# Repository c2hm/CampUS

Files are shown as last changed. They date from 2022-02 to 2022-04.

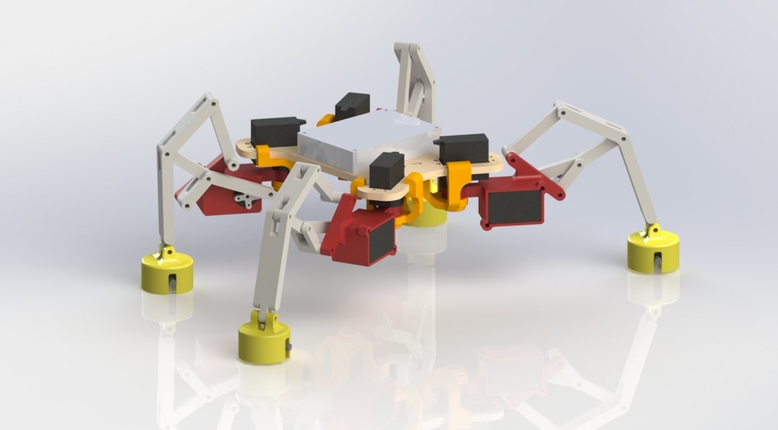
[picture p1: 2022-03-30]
Conception/Prototype #2/vue isometrique (2).JPG

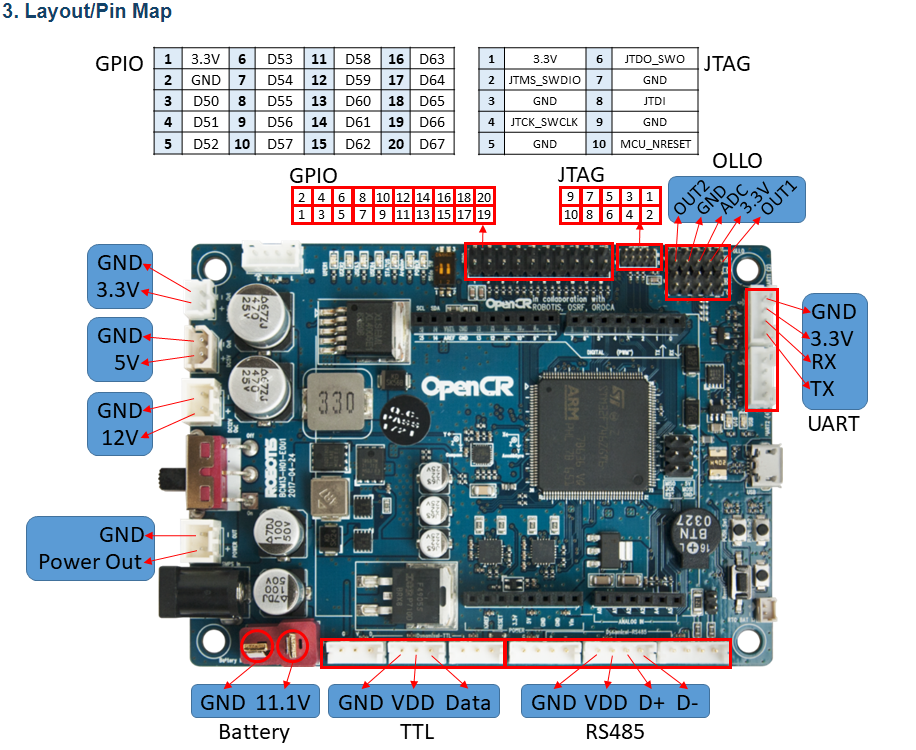
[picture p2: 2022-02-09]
Electricity/pins OpenCR.png

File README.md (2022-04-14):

# CampUS
University of Sherbrooke robotics project
  
  Isometric view
  
The CampUS robot is a quadriped articulated robot. Each leg is independent and contains two degrees of freedom, but all of these allow the robot to move from all sides.   An electromagnet is attached to each leg to allow the robot to move on metal surfaces. All components are controlled by an OpenCR card programmed in C++. This program handles the low-level commands needed for the move. A user interface is used to communicate to the robot the sequences of high-level movements to be executed according to the user's intention. A Bluetooth module makes it possible to make the wireless link between the two programs. 

The diagram below summarizes the general architecture explained above:

 

Here is a demonstration of the robot : 40 cm at 0°, 20 cm at 10° and 20 cm at -10°  

https://user-images.githubusercontent.com/61423054/163423675-e28aa425-6067-4ee7-8b0e-fbca73a94658.mp4

# Code

  This folder contains all the code for Python interface and the C++ Arduino controller code
  
# Conception 

  This folder contains all the prototypes created on SolidWorks and the complete assembly manual of the mechanical and electrical parts

# Demo 

  This folder contains all the videos of movement to see the motion in detail
  
# Electricity

  This folder contains the information about the OpenCR board, the protoboard and overall circuit connections
  
# Tests

  This folder contains the different test plans

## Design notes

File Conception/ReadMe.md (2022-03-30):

# Prototype #1
The first prototype has an elongated X body shape with the legs pointing in the elongated direction. This is making the robot really long especially because the position of the pivot point of the leg were towards the outside of the body. The shoulder are positioned over the frame making the robot really low profile.

# Prototype #2
In the second prototype, the shoulder are the part who changed the most. The pivot point has been moved toward the center of the frame so that the servo has been flipped. To acheived that the shoulder need to be moved under the frame. This make sure that the motor mount isn't to high to not interfere with the body. The frame has been reduced in size to just be large enough for the OpenCR card.

# Prototype #3
In the third iteration, a stopper has been added to the end of the leg to limit the movement of the magnet.

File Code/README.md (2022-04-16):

# Contents of the folders
    Arduino Code : Code for the openCR and the template on Arduino mega
    Pthon controller : Code for the user interface and setup of pyqt5 on pycharm

# Behavior of the robot 
Wake up of the robot : 

    Robot goes in default stance, activates magnets and waits for cmd
    
Python code point of view for the communications below :

    Mode 1 : Automatic

        Home button (default stance) : send home cmd
        wait for end message

        To add action : Input distance and angle and press add
        add up to 10 actions
        Then press start to send cmd
        wait for end message

    Mode 2 : Semi-automatic

        Home button (default stance) : send home cmd
        wait for end message

        Input angle and press enter to send cmd
        wait for end message

        button to go forward
        button to go backward
        In both case : send command to move when pressed and send cmd to stop when depressed
        Robot completes sequence before stopping
        wait for end message

    Mode 3 : Manual

        Home button (default stance) : send home cmd
        wait for end message

        For each motor : (4 stepper (0-180 deg) and 4 stepper (360 deg))
        Magnet of leg must be turned off
        Button to turn clockwise
        Button to turn anti-clockwise
        In both case : send command to move when pressed and send cmd to stop when depressed

        For each magnet :
        Check box to enable/disable
        To disable a magnet, at least 3 magnets must be enabled (security factor)
# Walking sequence:

1. Get to starting stance
2. Reset position variables
3. disable front-left magnet
4. front-left leg extends
5. enable front-left magnet
6. disable front-right magnet
7. front-right leg extends
8. enable front-right magnet
9. front legs retract while rear legs extend
10. disable rear-left magnet
11. rear-left leg retracts
12. enable rear-left magnet
13. disable rear-right magnet
14. rear-right leg retracts
15. enable rear-right magnet
16. repeat steps 3 to 15 until goal is reached

# State machine of the arduino code
Note that the automatic mode is a series of semi-automatic orders



# Communication protocol
The communication is based on the Robust Arduino Serial Protocol in Python:
https://github.com/araffin/python-arduino-serial

The protocol is based on a master and slave relation. Therefore the arduino only speaks to when it is talked to by the python controller.
This system insures that the communication is synchronized and that no message is lost. Also, all messages are 8bit which insures the arduino buffer serial will not overflow

There are two types of messages :

    Orders (8bit integer) : defines the type of request or response; can be immediately followed by a parameter 
    Parameters (8bit integer) : Optional number representing a precision of an order 
    Ex : Order : LEFT_MOTOR ; Parameter : 40; Output : Give a 40 rad/s speed to the motor
    
Sequence of communication :
 
   Paring: 
   The python controller sends order HELLO every few moments until a HELLO order is returned by the arduino.
   
   Action request order :
   Python controller sends order and waits for RECEIVED order returned by the arduino.
   Optional : Sends parameter and waits for RECEIVED order returned by the arduino.
   Python controller waits for finished order type of order returned by the arduino.
    
   Information request order :
   Python controller sends order and waits for RECEIVED order returned by the arduino.
   Python controller waits for parameter then sends RECEIVED order.
    
   If RECEIVED order is not received by the python controller, the order or paramter is either resent or an error is raised.
   
Diagramme sans nom

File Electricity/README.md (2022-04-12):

Our electrical circuit is composed of the openCR board, a custom protoboard and an arduino nano. The openCr board is the master board of the circuit that deals with communicating and giving orders to the different components. The protoboard contains the circuit and the parts necessary for the proper functioning of the components. The arduino nano is used to receive a 3.3V signal and send a 5V signal back to the mosfets.

About the Arduino plugins:

Each pins has a maximum output current of 5mA. Total output current from pins should not reach over ±120mA

Arduino's already used pins by openCR:
 - 13

About the OpenCR plugins:

The total power consumption on 12V and 5V ports should not exceed 55W.

About the circuit: 

The 12V port is used with the mosfet to give power for the electromagnets.

Two TTL ports is used for the motors. (multiple or just one can be used)

The 5V port is used for the servomotors. (Power input)

Module Bluetooth : 

Model : HC-05

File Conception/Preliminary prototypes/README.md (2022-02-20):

There are the two different model of legs that were considered at the start of this project.
The Crab leg style as been choosed to further development.
The directory Prototype #1 and #2 are the iteration of it

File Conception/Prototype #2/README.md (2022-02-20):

Here are the files of the 2nd prototype.

There is the STl file for 3D printing and the DXF file for the laser cut of the frame

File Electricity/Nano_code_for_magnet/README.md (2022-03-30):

An arduino nano is necessaty to transform the 3.3 v of the openCR to 5 V for the trigger pins of the mosfets.
5 V is more secure for the activation of the mosfets.
A level-shifter could also have been used.

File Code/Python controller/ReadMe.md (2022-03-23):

UI features (object) names:

Automatic page:

	Buttons:
		Home button: pb_home_auto
		Start button: pb_start
		Stop button: pb_stop
		Add command button: pb_addcmd
		
	Label:
		State label: label_state_auto
		State command list: label_cmdlist
		
	Text edits:
		Distance text edit: distance_input
		Angle text edit: angle_input_auto
		
	Ckeckbox:
		Reverse checkbox: cb_reverse

Semi-Automatic:

	Buttons:
		Home button: pb_home_semi
		Send command button: pb_sendcmd
		Jog foward button: pb_jogf
		Job backward button: pb_jogb
		
	Label:
		State label: label_state_semi
		
	Text edit:
		angle text edit: angle_input_semi
		
Manual:

	Buttons:
		Steppers:
			Front left clockwise button: pb_step_flclock
			Front left counter button: pb_step_flcounter
			
			Front right clockwise button: pb_step_frclock
			Front right counter button: pb_step_frcounter
			
			Back left clockwise button: pb_step_blclock
			Back left counter button: pb_step_blcounter
			
			Back right clockwise button: pb_step_brclock
			Back right counter button: pb_step_brcounter
			
		Servos:
			Front left clockwise button: pb_ser_flclock
			Front left counter button: pb_ser_flcounter
			
			Front right clockwise button: pb_ser_frclock
			Front right counter button: pb_ser_frcounter
			
			Back left clockwise button: pb_ser_blclock
			Back left counter button: pb_ser_blcounter
			
			Back right clockwise button: pb_ser_brclock
			Back right counter button: pb_ser_brcounter
	CheckBox:
		Magnets:
			Front left checkbox: cb_flmag
			Front right checkbox: cb_frmag		
			Back left checkbox: cb_blmag
			Back right checkbox: cb_brmag

Next step:

    Automatic:
        Finish home
        State window
        Start/Stop
        Check mark
    
    Semi-auto:
        Jog 
        Send command

    Manual:
        Button
        Check mark
    
    Bug:
        Prevent the user to press any button while sending information
        Prevent the user to enter letter in the text input
	Always open the automatic page when the code is run

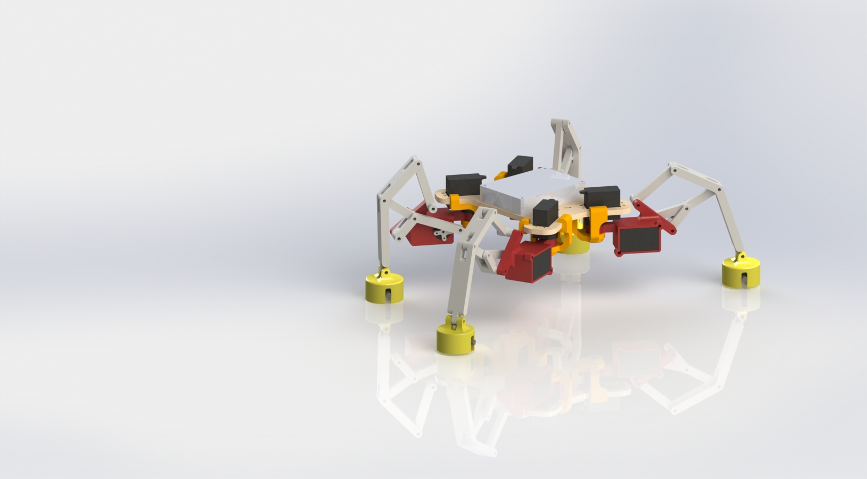
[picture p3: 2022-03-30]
Conception/Prototype #2/Isometric view.JPG

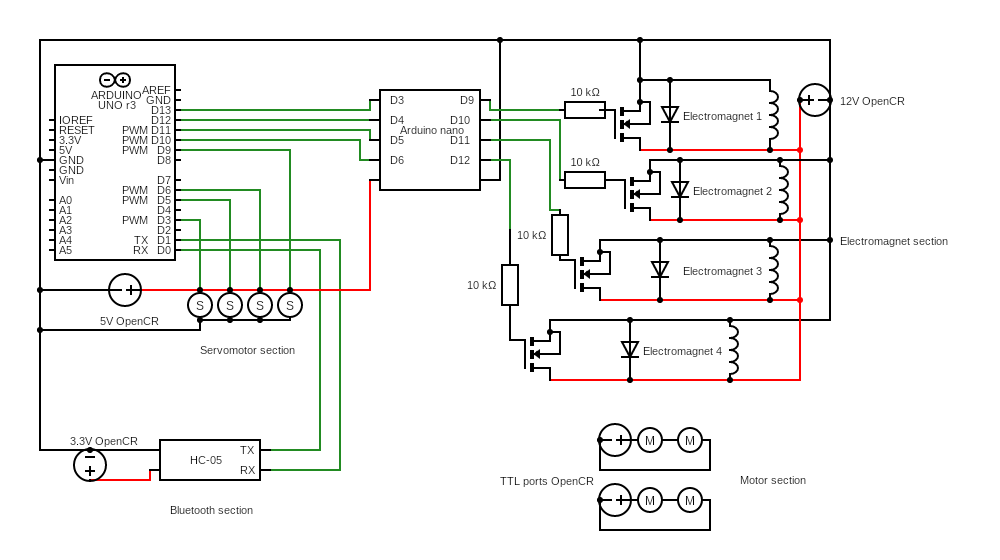
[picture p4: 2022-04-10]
Electricity/circuit.png

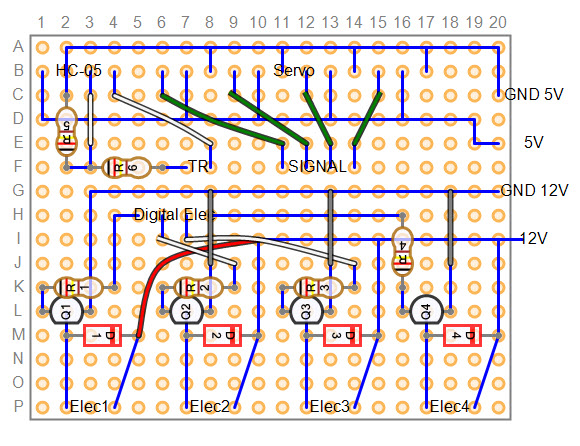
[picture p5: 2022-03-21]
Electricity/Protoboard.jpg

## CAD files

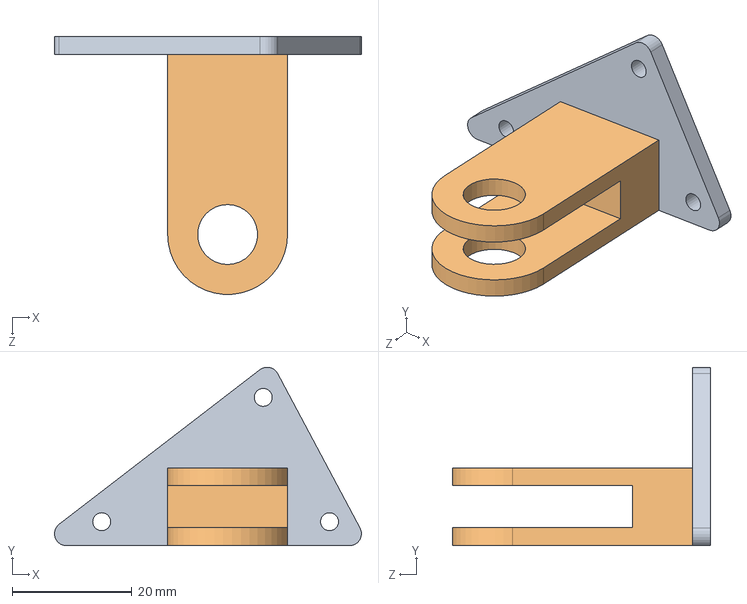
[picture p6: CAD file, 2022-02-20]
Conception/Preliminary prototypes/Crab leg/CRAB-010.SLDASM
51.2 x 29.8 x 43.0 mm
CRAB-006
Epaule

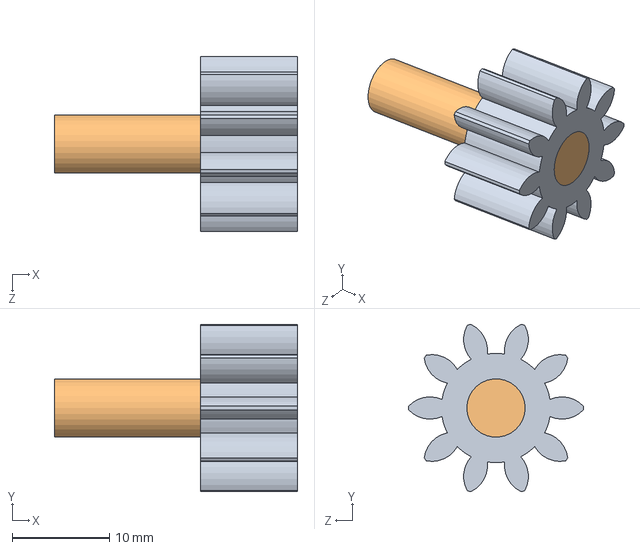
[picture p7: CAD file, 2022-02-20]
Conception/Preliminary prototypes/Rack leg/gear.SLDASM
25.0 x 17.2 x 18.0 mm
spur gear_am
tige moteur

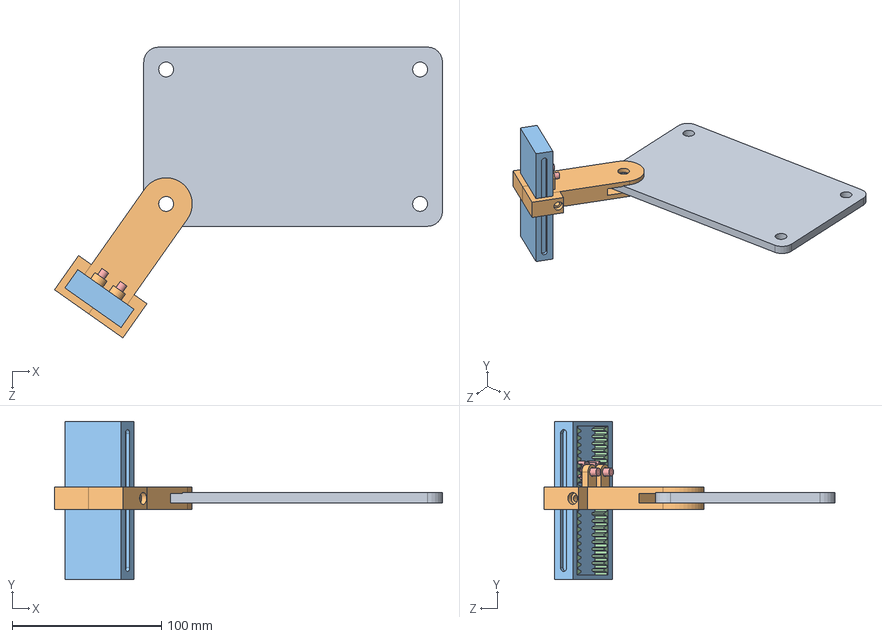
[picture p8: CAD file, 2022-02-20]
Conception/Preliminary prototypes/Rack leg/Rack leg.SLDASM
259.7 x 106.0 x 194.7 mm
Arm
Empty leg
rack spur rectangular_am x 2
spur gear_am x 2

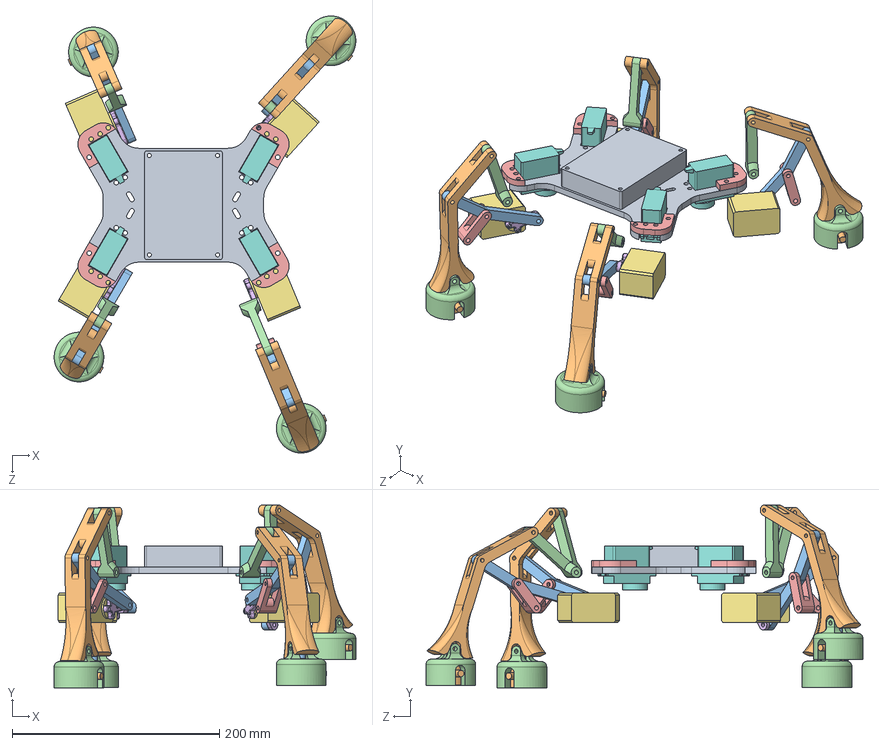
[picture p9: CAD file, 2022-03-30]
Conception/Prototype #2/Prototype #2.SLDASM
291.4 x 176.6 x 422.1 mm
Frame-02
Leg-02 x 4
Link 1-02 x 4
Link 2-02 x 4
Link 3-02 x 4
Motor attachement-02 x 4
Dynamixel XL430-W250-T x 4
servo x 4
OpenCR card
5698K112_DC-Powered Electromagnet x 4
91251A342_Black-Oxide Alloy Steel Socket Head Screw x 4
Magnet ring x 4
Servo support x 4

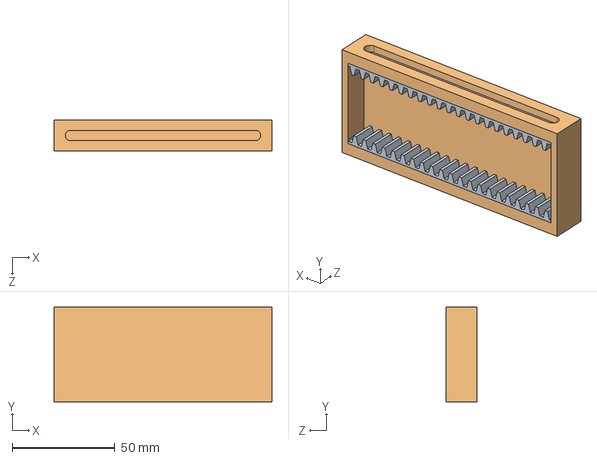
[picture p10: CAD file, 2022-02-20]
Conception/Preliminary prototypes/Rack leg/Leg.SLDASM
106.0 x 46.0 x 15.0 mm
rack spur rectangular_am x 2
Bras 2

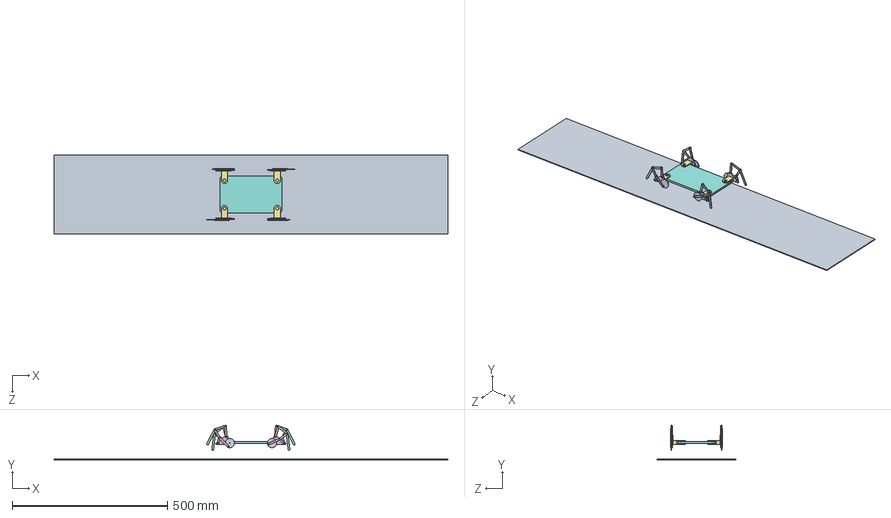
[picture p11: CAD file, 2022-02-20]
Conception/Preliminary prototypes/Crab leg/Corps et crab.SLDASM
1270.0 x 111.6 x 254.0 mm
CRAB-001 x 4
CRAB-002 x 4
CRAB-003 x 4
CRAB-004 x 4
CRAB-005 x 4
CRAB-006 x 4
Epaule x 4
plaque

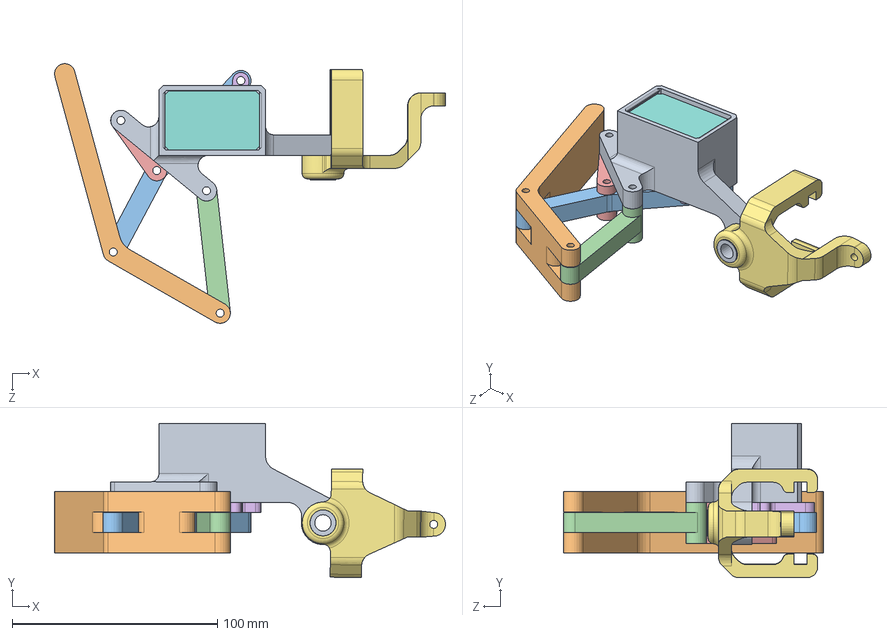
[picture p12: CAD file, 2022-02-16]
Conception/Prototype #1/Leg assembly.SLDASM
190.6 x 75.2 x 126.6 mm
Motor mount
Leg
Link 1
Link 2
Link 3
Motor attachement
Servo mount
Motor

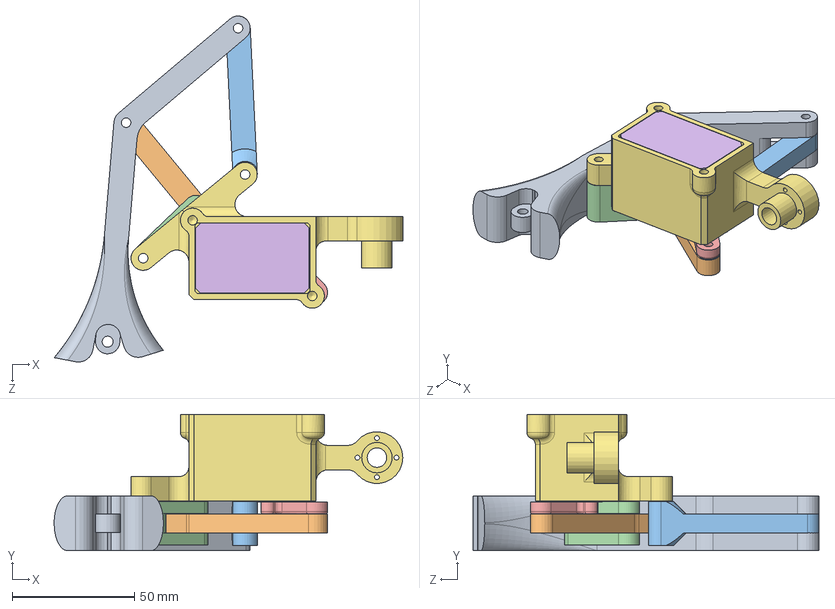
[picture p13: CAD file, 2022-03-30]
Conception/Prototype #2/Leg assembly-02.SLDASM
142.8 x 55.9 x 141.7 mm
Leg-02
Link 1-02
Link 2-02
Link 3-02
Motor attachement-02
Dynamixel XL430-W250-T
Symetry of Motor mount-02

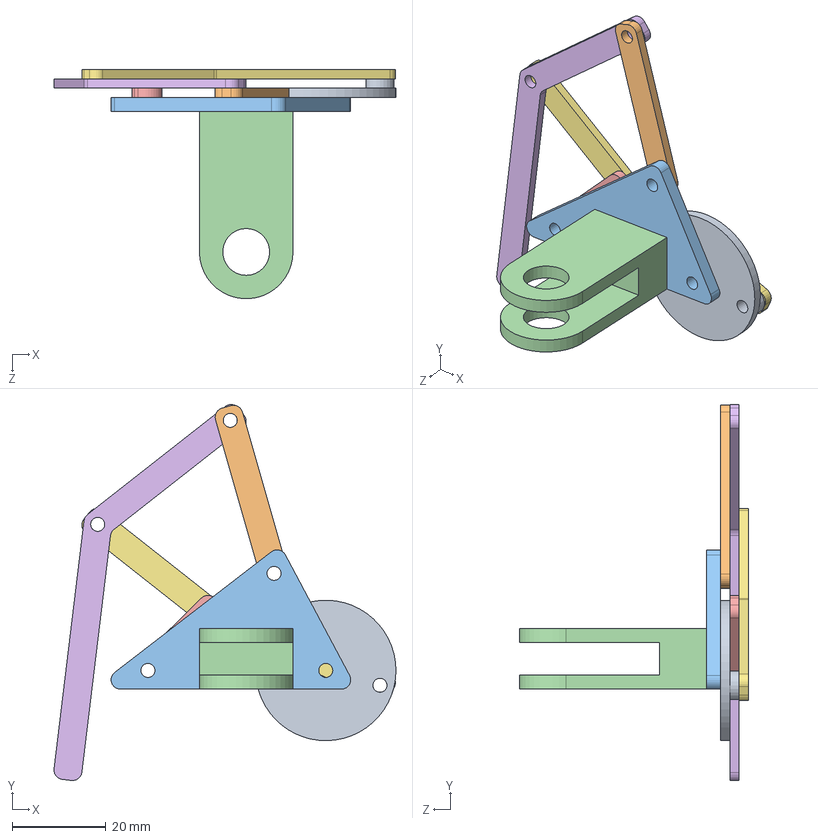
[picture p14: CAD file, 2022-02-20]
Conception/Preliminary prototypes/Crab leg/CRAB-100.SLDASM
73.1 x 80.3 x 49.0 mm
CRAB-001
CRAB-002
CRAB-006
Epaule
CRAB-003
CRAB-004
CRAB-005

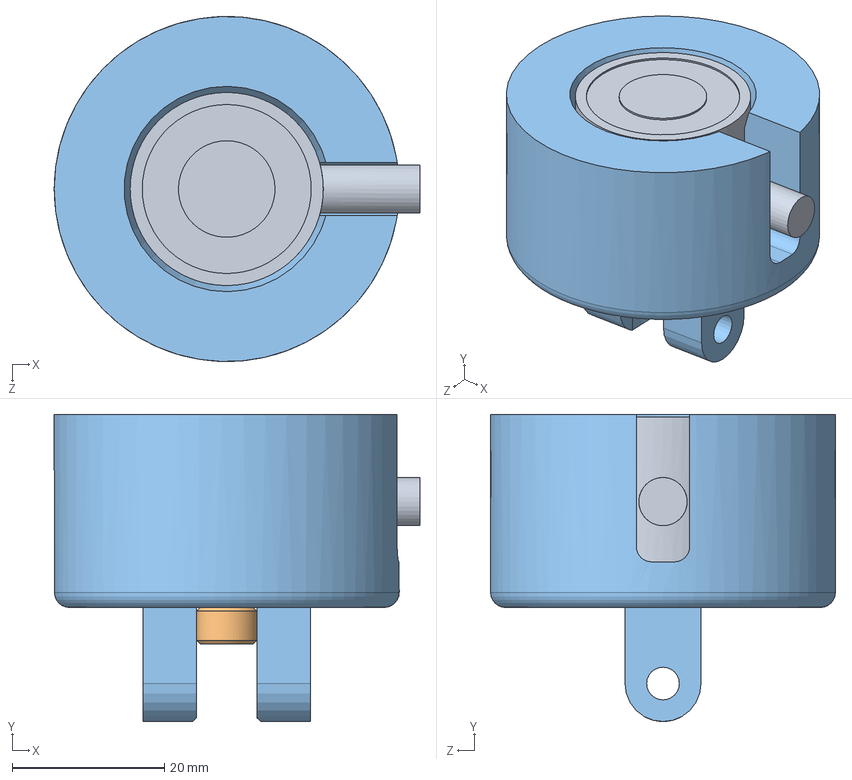
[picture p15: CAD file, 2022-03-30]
Conception/Prototype #2/Magnetic feet.SLDASM
48.1 x 40.4 x 45.4 mm
5698K112_DC-Powered Electromagnet
91251A342_Black-Oxide Alloy Steel Socket Head Screw
Magnet ring

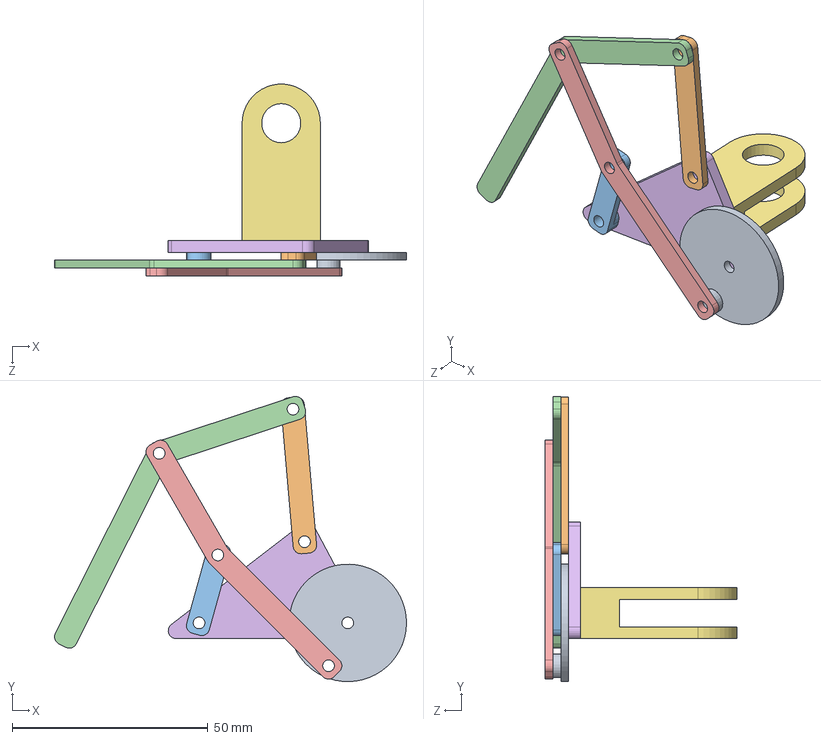
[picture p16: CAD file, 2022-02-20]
Conception/Preliminary prototypes/Crab leg/CRAB-000.SLDASM
89.9 x 72.9 x 49.0 mm
CRAB-001
CRAB-002
CRAB-003
CRAB-004
CRAB-005
CRAB-006
Epaule

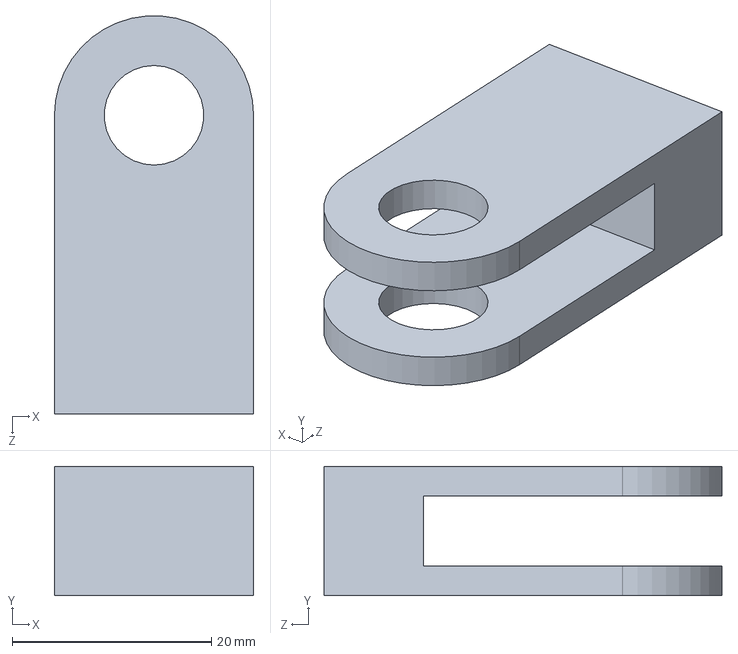
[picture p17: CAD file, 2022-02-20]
Conception/Preliminary prototypes/Crab leg/Shoulder.SLDPRT
20.0 x 13.0 x 40.0 mm

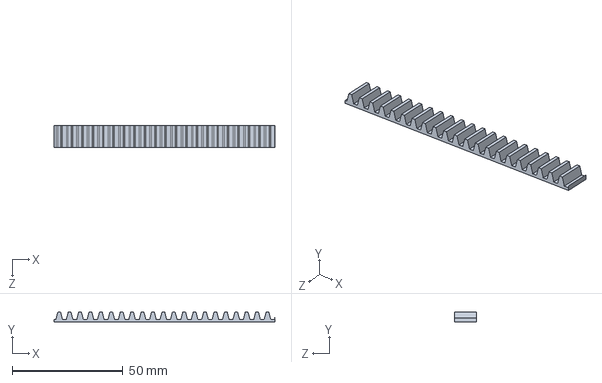
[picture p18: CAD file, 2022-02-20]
Conception/Preliminary prototypes/Rack leg/rack spur rectangular_am.SLDPRT
100.0 x 4.50 x 10.0 mm

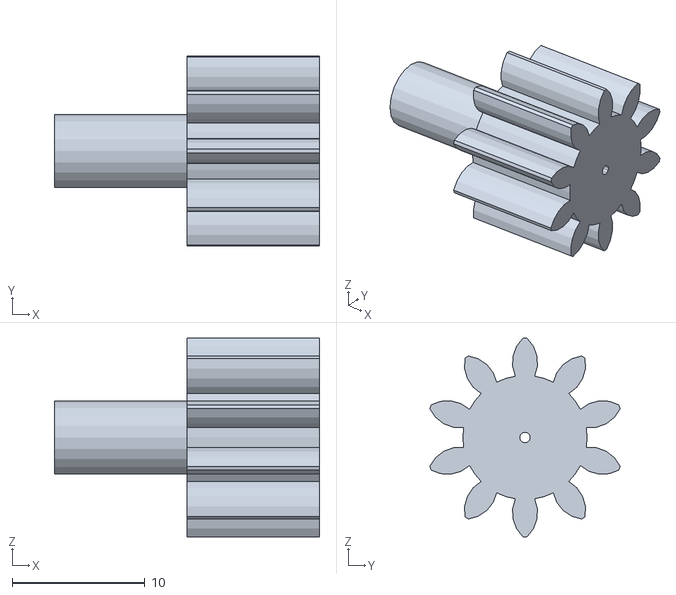
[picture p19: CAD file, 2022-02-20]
Conception/Preliminary prototypes/Rack leg/STL/Gear 1.25.STL
20.0 x 14.4 x 15.0

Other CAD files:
Conception/Preliminary prototypes/Crab leg/CRAB-011.SLDASM
Conception/Preliminary prototypes/Crab leg/STL/CRAB-010 reverse.stl
Conception/Prototype #1/Motor mount.sldprt
Conception/Prototype #2/Link 3-02.sldprt
Conception/Preliminary prototypes/Crab leg/Body.SLDPRT
Conception/Preliminary prototypes/Crab leg/CRAB-001.SLDPRT
Conception/Preliminary prototypes/Crab leg/CRAB-002.SLDPRT
Conception/Preliminary prototypes/Crab leg/CRAB-003.SLDPRT
Conception/Preliminary prototypes/Crab leg/CRAB-004.SLDPRT
Conception/Preliminary prototypes/Crab leg/CRAB-005.SLDPRT
Conception/Preliminary prototypes/Crab leg/CRAB-006.SLDPRT
Conception/Preliminary prototypes/Crab leg/Plate.SLDPRT
Conception/Preliminary prototypes/Crab leg/STL/CRAB-001.STL
Conception/Preliminary prototypes/Crab leg/STL/CRAB-002.STL
Conception/Preliminary prototypes/Crab leg/STL/CRAB-003.STL
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

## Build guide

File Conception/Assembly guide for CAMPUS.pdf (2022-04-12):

# Assembling guide of the campus robot

Number given to the items | Item | Description | Quantity needed
1 | DC-Powered Electromagnet | 5698K112* | 4
2 | Screw no 1 | 91251A342* | 4
3 | Magnet ring | Receptacle for the magnet | 4
4 | Leg | | 4
5 | Link-1 | Connects the leg to the motor | 4
6 | Link-2 | Connects the leg to the motor | 4
7 | Link-3 | Connects the leg to the motor | 4
8 | Motor attachment | Connects the leg to the motor | 4
9 | Motor | DYNAMIXEL XL430-W250-T | 4
10 | Motor mount | Receptacle for the motor | 4
11 | Servo mount | Receptacle for the servomotor | 4
12 | Servomotor | | 4
13 | Frame | Main piece for carrying the legs | 1
14 | Servo support | Makes sur the leg is fixed | 4

*Numbers in the item description refers to Mcmaster-Carr numbers

# 1-foot assembly

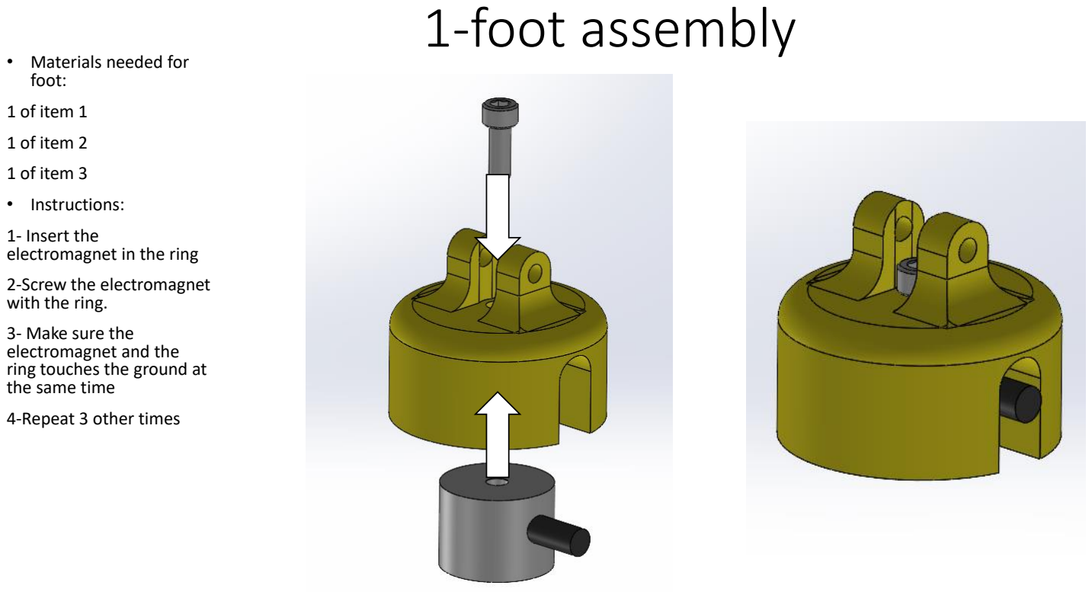
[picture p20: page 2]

- Materials needed for
foot:
1 of item 1
1 of item 2
1 of item 3
- Instructions:
1- Insert the
electromagnet in the ring
2-Screw the electromagnet
with the ring.
3- Make sure the
electromagnet and the
ring touches the ground at the same time
4-Repeat 3 other times

# 2-leg assembly part 1 • Materials needed for

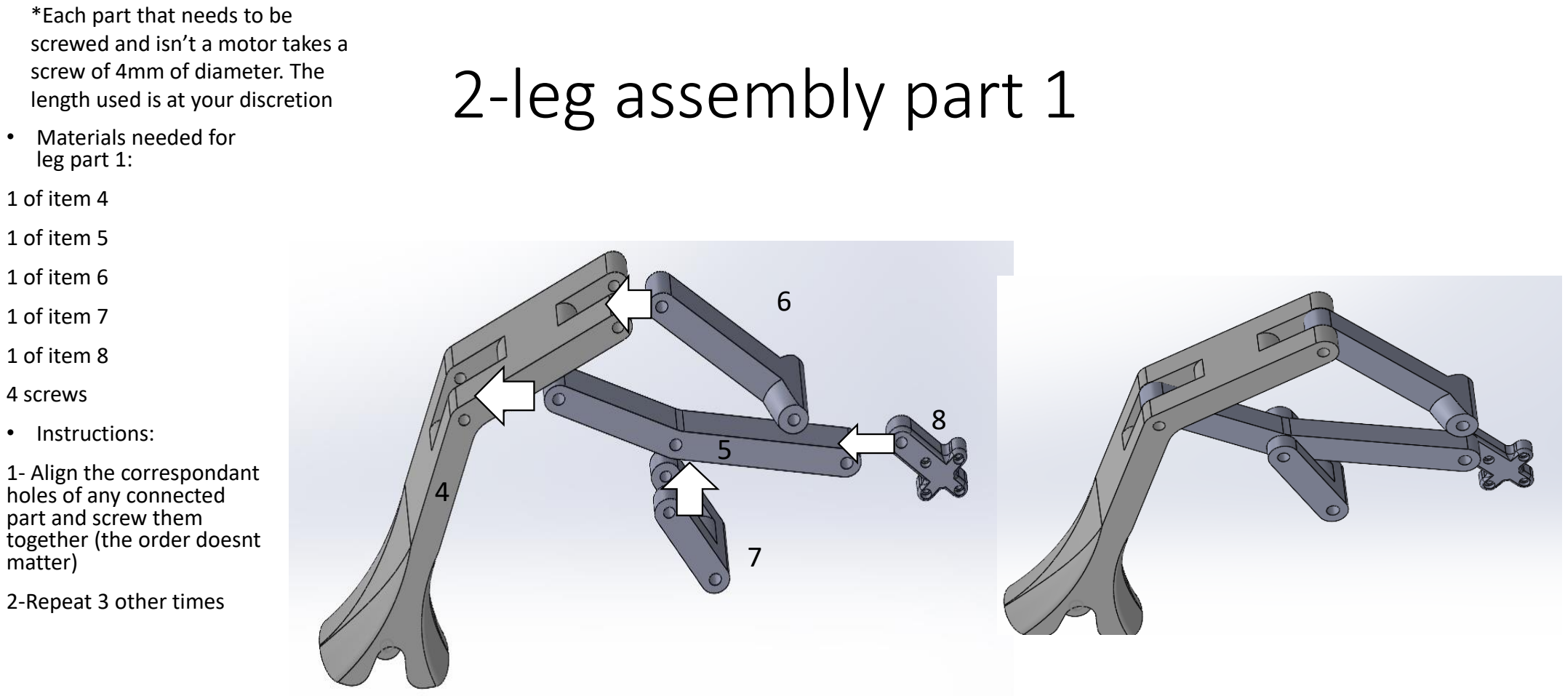
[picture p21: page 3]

leg part 1:
1 of item 4
1 of item 5
1 of item 6
1 of item 7
1 of item 8
4 screws
- Instructions:
1- Align the correspondant holes of any connected
part and screw them
together (the order doesnt matter)
2-Repeat 3 other times

*Each part that needs to be screwed and isn’t a motor takes a screw of 4mm of diameter. The length used is at your discretion

8

7

6

5
4

# 4-leg assembly part 2 • Materials needed for

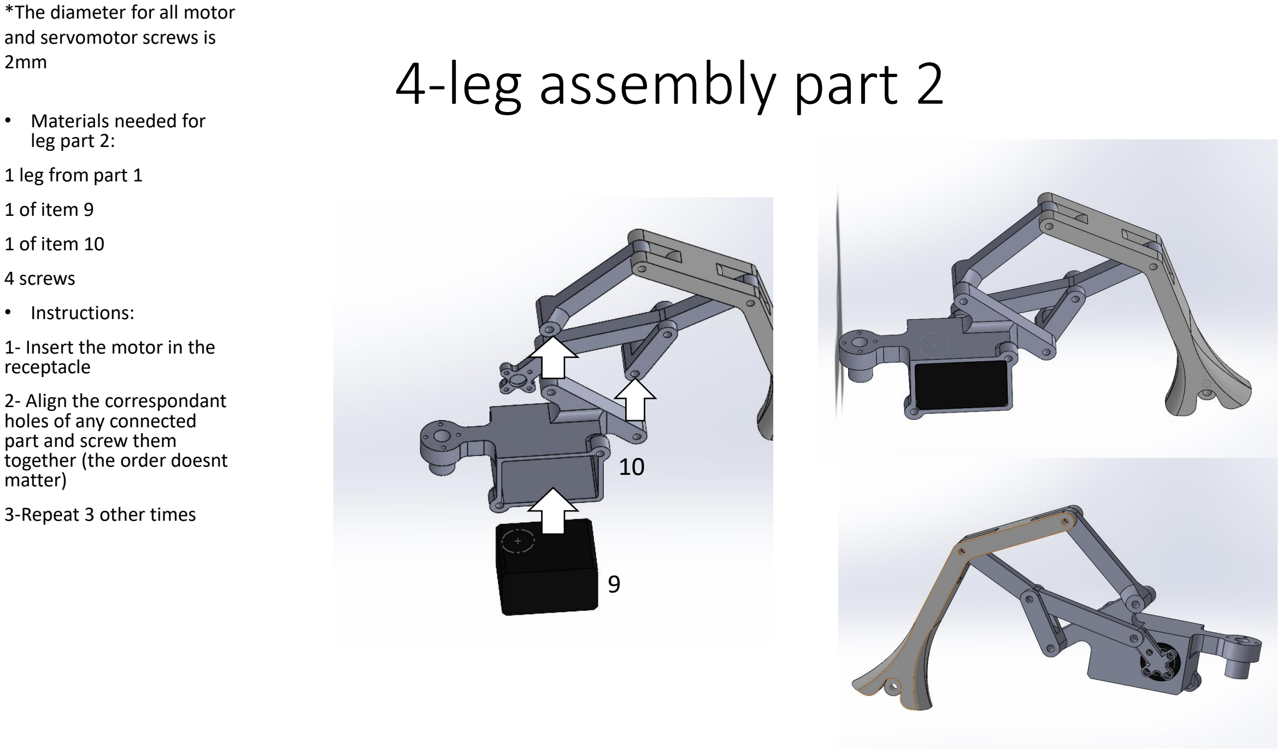
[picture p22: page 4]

leg part 2:
1 leg from part 1
1 of item 9
1 of item 10
4 screws
- Instructions:
1- Insert the motor in the receptacle
2- Align the correspondant holes of any connected
part and screw them
together (the order doesnt matter)
3-Repeat 3 other times

9

10

*The diameter for all motor and servomotor screws is
2mm

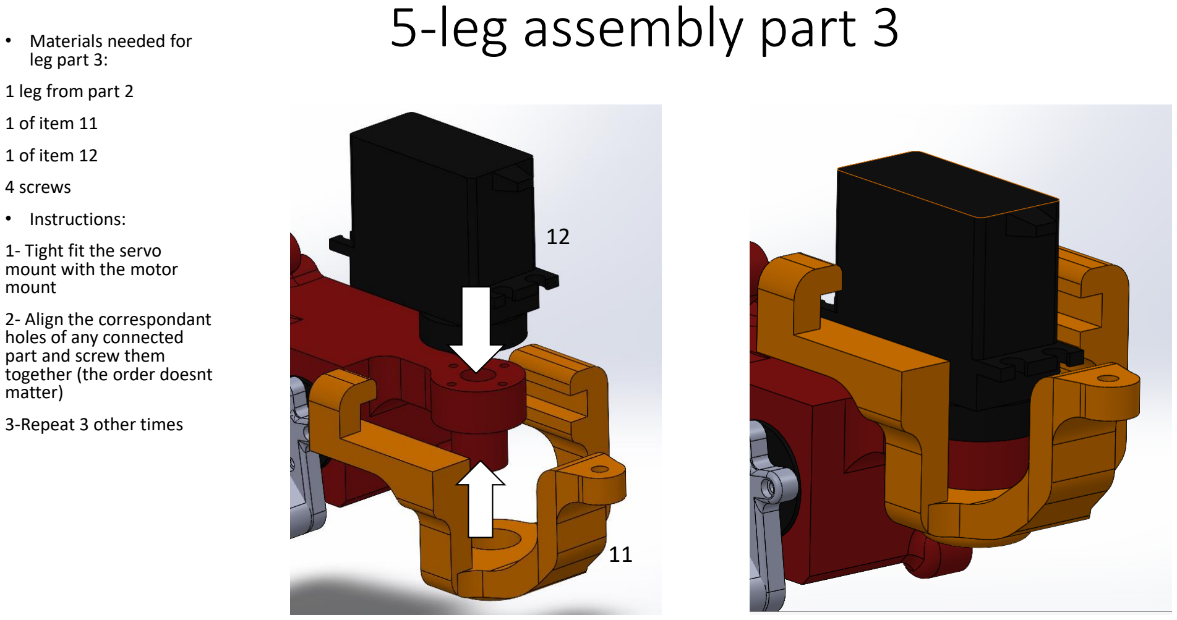
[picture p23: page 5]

- Materials needed for | 5-leg assembly part 3 leg part 3:

1 leg from part 2
1 of item 11
1 of item 12
4 screws
- Instructions:
1- Tight fit the servo
mount with the motor
mount
2- Align the correspondant holes of any connected
part and screw them
together (the order doesnt matter)
3-Repeat 3 other times

11

12

# needed for leg 6-leg assembly part 4

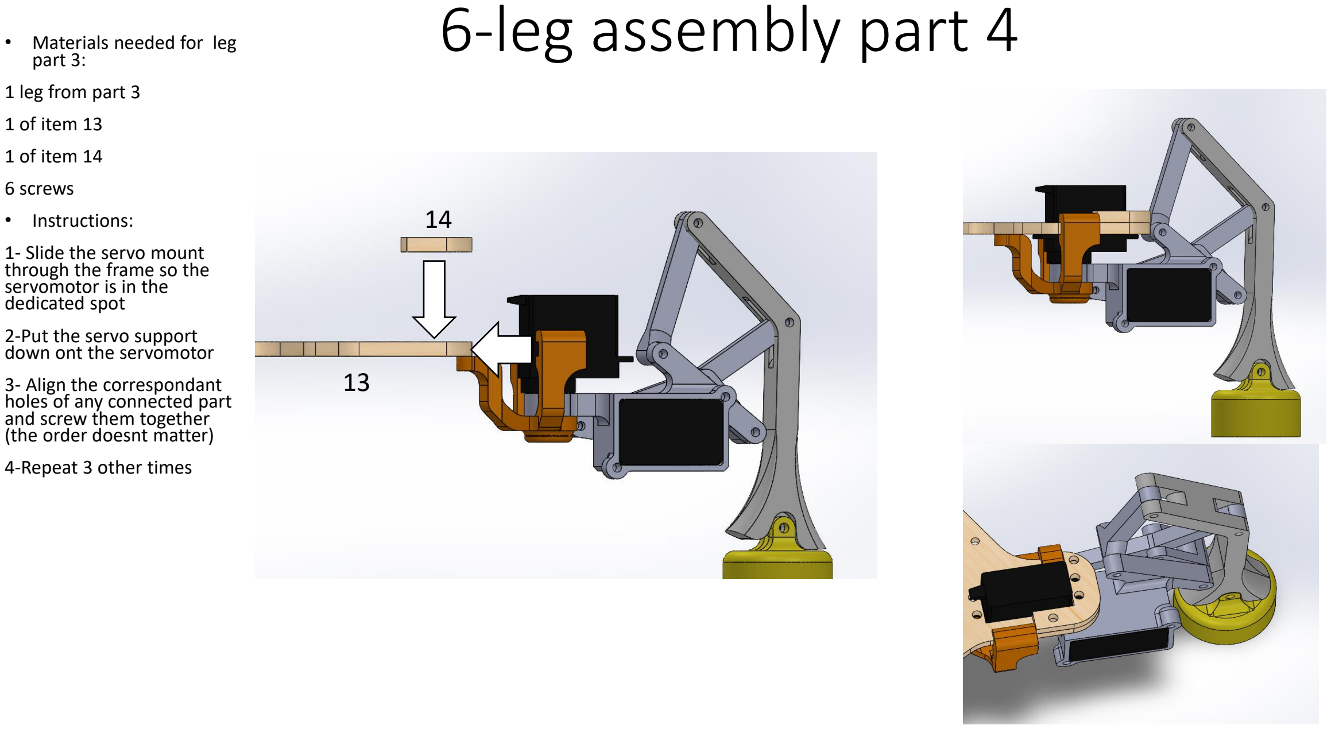
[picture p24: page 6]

- Materials
part 3:
1 leg from part 3
1 of item 13
1 of item 14
6 screws
- Instructions:
1- Slide the servo mount
through the frame so the
servomotor is in the
dedicated spot
2-Put the servo support
down ont the servomotor
3- Align the correspondant holes of any connected part and screw them together
(the order doesnt matter)
4-Repeat 3 other times

13

14

# 7-Result without open cr card

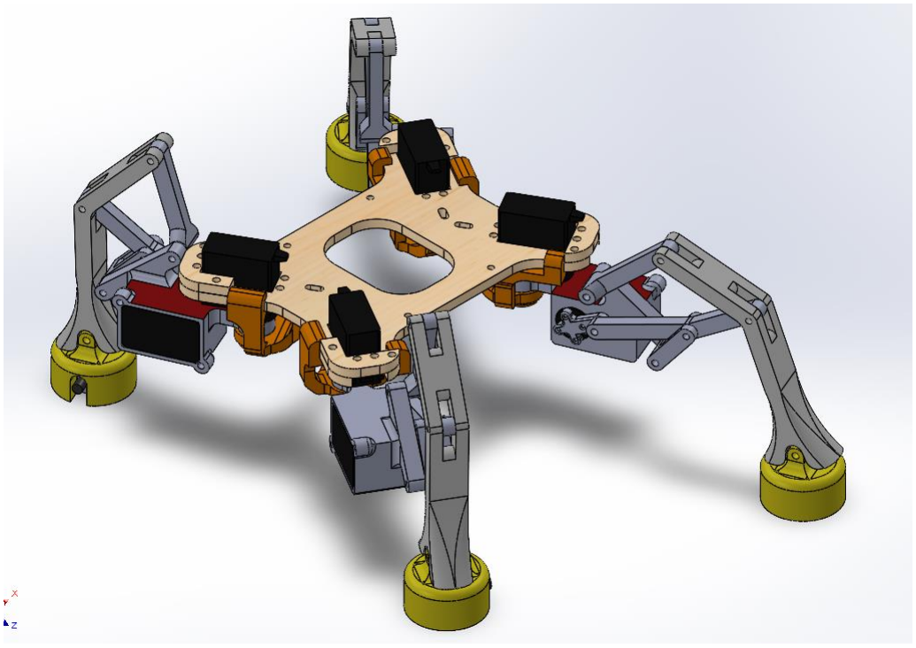
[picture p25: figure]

# Electrical assembly guide

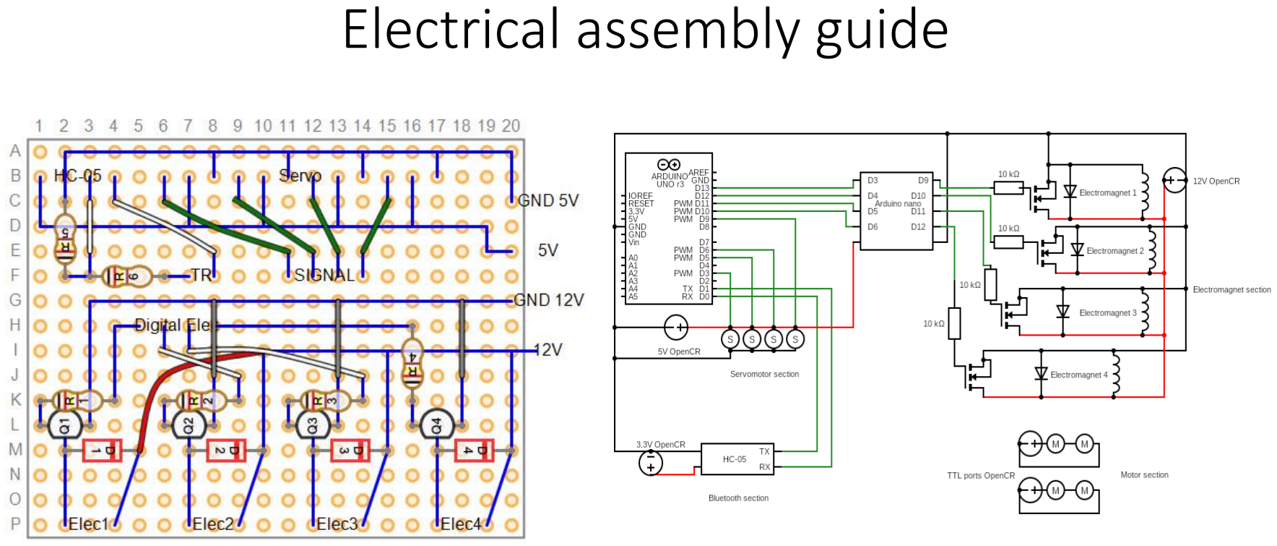
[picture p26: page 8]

# List of Items used for the protoboard

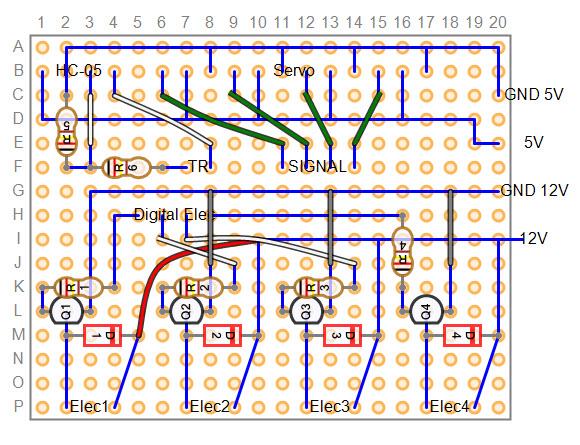
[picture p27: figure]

Item | Description | Quantity needed
Mosfet | IRFZ44N | 4
Resistor for electromagnets | 10kΩ | 4
Diode | 1N4007 | 4
Terminal block for pcb | 2 screws | 4

# 1- Explanations about previous images

# - You can base yourself on the previous photos to do the electrical assembly, just mind that depending on your open cr card, some pins might not work. You can change them as necessary, just remember to

change the code later depending on your choices.

### *Note that a tension divider as been installed for the bluetooth which is useless. We thought the openCR pins were 5V but they are 3.3V so it’s safe to plug the bluetooth directly to the

openCR card.

2

# - IRL demo of the protoboard

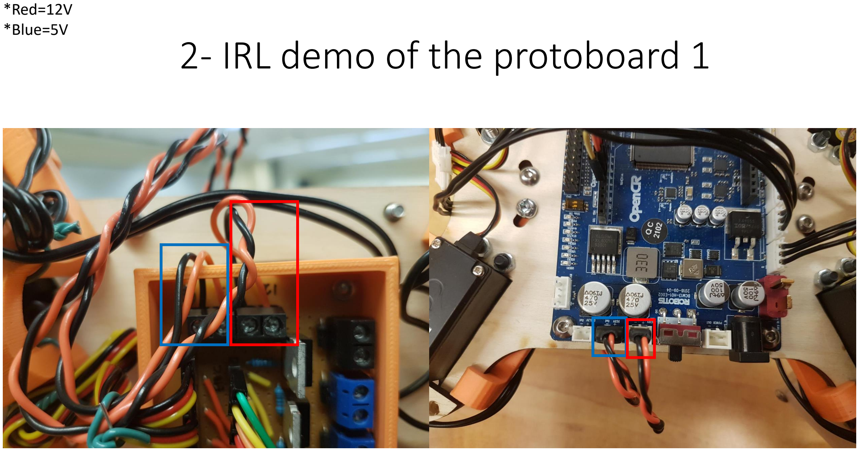
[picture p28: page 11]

1

### *Red=12V *Blue=5V

# 2- IRL demo of the protoboard 2

### *Red=Motor

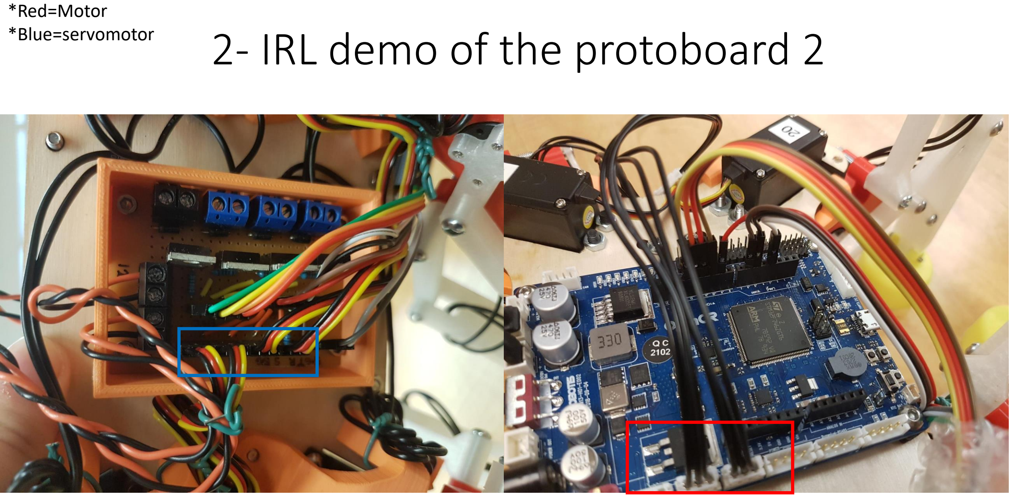
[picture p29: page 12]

### *Blue=servomotor

# 2- IRL demo of the protoboard 3

### *Red=signals for

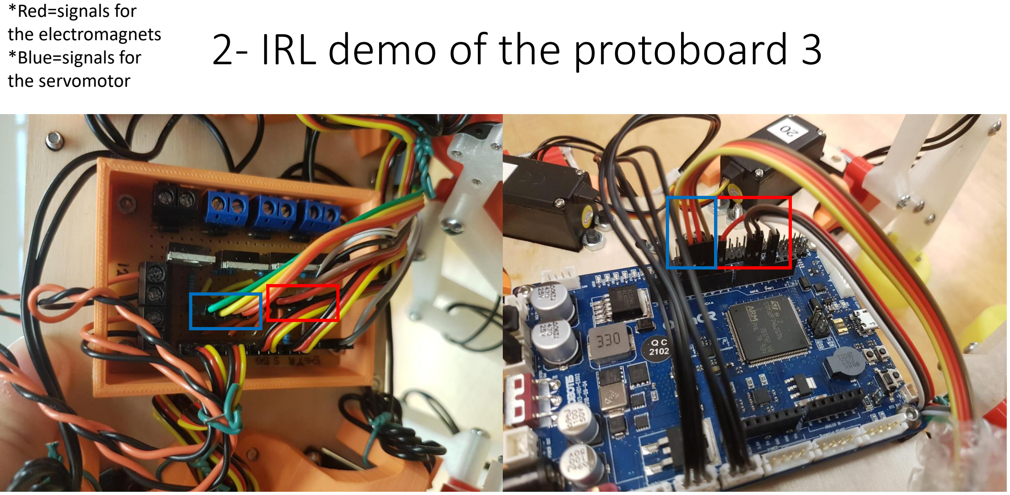
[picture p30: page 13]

### the electromagnets *Blue=signals for the servomotor

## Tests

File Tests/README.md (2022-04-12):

To ensure the proper working of each of the project elements, four test plans were made: electrical, interface, communication and integration. The electrical test plan tests the assembly of the Protoboard by analyzing the response of the electromagnets and servomotors. The interface test plan mainly ensures that it does not crash when several buttons are pressed at the same time. In addition, the user cannot send orders with letters or special characters. The communication test plan checks that all commands sent by the interface are received by the master code and sends back an acknowledgment of receipt to the interface. Finally, the integration test plan is a mix between that of the interface and the communication but we replace the last by the robot. It is therefore verifying whether the robot reacts well to the commands of the interfaces.

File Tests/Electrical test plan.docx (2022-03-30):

These are the tests to verify the functionality of the electrical connections on the proto board.

Front-left (FR), front-right (FR), rear-left (RL), rear-right (RR)

# Test | Name | Description | Result | Success

1 | Simple electromagnet | One by one, the digital pins of the transistors are put on high for 2 seconds, then on low. (FL, FR, RL, RR) | Each electromagnet is on for 2 seconds, then completely off. (FL, FR, RL, RR) | YES
2 | Two electromagnets | The digital pins of two transistors are put on high for 2 seconds, then on low. The process is repeated for the other two. (FL - FR, RL - RR) | FL and FR are on for 2 seconds, then completely off. RL and RR are on for 2 seconds, then completely off. | YES
3 | All electromagnets | The digital pins of all the transistors are put on high for 5 seconds, then on low. | All the electromagnets are on for 5 seconds, then completely off. | YES
4 | Simple angular servos | One by one, the servos are assigned to 90°, then to 110°. (FL, FR, RL, RR) | One by one, each servo goes to 90°, the to 110° (FL, FR, RL, RR) | YES
5 | All angular servos | All the servos are assigned to 90°, then to 110° | All the servos go to 90°, then to 110° | YES
6 | All electromagnets and simple servos | The digital pins of all the transistors are put on high. Redo test #4. Then put the transistors pins on low after 5 seconds. | All the electromagnets are on while results of test #4 are occurring, Then, after 5 seconds, the electromagnets are completely off. | YES

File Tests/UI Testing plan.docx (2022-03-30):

# Test | Name | Description | Result | Succes

1 | Prevent text | Don't allow the user to input text for the distance and angle command | The interface ask to enter an interger whenever a command is added and letters figure in the input box. Thus, the input is discarded | Yes
2 | Prevent other command | Don't allow the user to press any other command button (home, start,stop and send command) | The UI is disabled when one of those button is pressed. | Yes
3 | Limit command number | A maximum of 6 command can be entered | When the user try to enter a 7th it discard it and tell the user that the list is full | Yes
4 | Disable UI | Do not start any command when the UI is disabled | It works, but because our button are initialized with connect.clicked the UI remember that a button was clicked so the command start after the previous one finished | No
5 | Servo angle | Limit the rotation of the servo because of physic limitation | When you enter an angle out off the -25 to 30 degree range an error indicate that the angle is out of reach | Yes

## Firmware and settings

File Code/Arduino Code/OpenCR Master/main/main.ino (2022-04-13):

//https://www.instructables.com/Cheap-2-Way-Bluetooth-Connection-Between-Arduino-a/

#include <Arduino.h>
#include "order.h"
#include "parameters.h"
#include "slave.h"
#include <Servo.h>
#include <Dynamixel2Arduino.h>
#include "definitions.h"
#include "functions.h"


//Prototypes
void get_messages_from_serial();
void homeMaster();
int get_param();
void auto_distance(int dist);
void auto_reverse(int dist);
void set_angle(int paramAngle);
void semi_auto_state(int state);
void servo_avant_droit(int state);
void servo_avant_gauche(int state);
void servo_arriere_droit(int state);
void servo_arriere_gauche(int state);
void moteur_avant_droit(int state);
void moteur_avant_gauche(int state);
void moteur_arriere_droit(int state);
void moteur_arriere_gauche(int state);
void electroaimant_avant_droit(int state);
void electroaimant_avant_gauche(int state);
void electroaimant_arriere_droit(int state);
void electroaimant_arriere_gauche(int state);

bool is_connected = false; ///< True if the connection with the master is available

int ERROR_PARAM = -1000;

void setup() {

  Serial.begin(9600);//Pour bluetooth deacendre a 9600, code python aussi

  // Wait until the arduino is connected to master
  while(!is_connected)
  {
    get_messages_from_serial();
  }
  init(servomotors,dxl);
}

void loop() 
{
  get_messages_from_serial();
  
}

/********************************************
 * 
 * Communication processing
 * 
 * ********************************************/
void get_messages_from_serial()
{
  if(Serial.available() > 0)
  {
    // The first byte received is the instruction
    Order order_received = read_order();

    if(order_received == HELLO)
    {
      // If the cards haven't say hello, check the connection
      if(!is_connected)
      {
        is_connected = true;
        write_order(HELLO);
      }
      else
      {
        // If we are already connected do not send "hello" to avoid infinite loop
        write_order(ALREADY_CONNECTED);
      }
    }
    else if(order_received == ALREADY_CONNECTED)
    {
      is_connected = true;
    }
    else
    {
      //Processes the order
      switch(order_received)
      {
        case HOME:
        {
          write_order(RECEIVED);
          homeMaster();
          break;
        }

        case AUTO_DISTANCE:
        {
          //reads parameter
          write_order(RECEIVED); 

          int dist = get_param();
          Serial.flush(); //avoid multiple instaces of param in serial
          
          if (dist >= -1000 && dist <= 1000)
          {
            write_order(RECEIVED); 
            auto_distance(dist);
          
          }
          else 
          {
            write_order(ERROR1); 
          }
          

          break;
        }

        case AUTO_REVERSE:
        {
          write_order(RECEIVED); 

          int dist = get_param();
          Serial.flush(); //avoid multiple instaces of param in serial
          
          if (dist >= -1000 && dist <= 1000)
          {
            write_order(RECEIVED); 
            auto_reverse(dist);
          
          }
          else 
          {
            write_order(ERROR1); 
          }
  
          break;
        }

        case ANGLE:
        {
          write_order(RECEIVED);

          //reads parameter
          angle = get_param();
          Serial.flush(); //avoid multiple instaces of param in serial

          if (angle >= -25 && angle<=25)
          {
            write_order(RECEIVED); 
            set_angle(angle);
          }
          else 
          {
            write_order(ERROR1); 
          }
          break;
        }

        case SEMI_AUTO_STATE:
        {
          write_order(RECEIVED);

          //reads parameter
          int state = get_param();
          Serial.flush(); //avoid multiple instaces of param in serial

          if (state==-1 || state==1)
          {
            write_order(RECEIVED); 
            semi_auto_state(state);
          
          }
          else 
          {
            write_order(ERROR1); 
          }
 
          break;
        }


        case SERVO_AVANT_DROIT:
        {

          write_order(RECEIVED); 

          //reads parameter
          int state = get_param();
          Serial.flush(); //avoid multiple instaces of param in serial

          if (state == -1 || state==1)
          {
            write_order(RECEIVED); 
            servo_avant_droit(state);
          }
          else 
          {
            write_order(ERROR1); 
          }
        break;
        }
        
        case SERVO_AVANT_GAUCHE:
        {

          write_order(RECEIVED); 

          //reads parameter
          int state = get_param();
          Serial.flush(); //avoid multiple instaces of param in serial
           if (state == -1 || state==1)
          {
            write_order(RECEIVED); 
            servo_avant_gauche(state);
          }
          else 
          {
              
            write_order(ERROR1);
          }
        
          break;
        }

        case SERVO_ARRIERE_DROIT:
        {

          write_order(RECEIVED); 

          //reads parameter
          int state = get_param();
          Serial.flush(); //avoid multiple instaces of param in serial
          if (state == -1 || state==1)
          {
            write_order(RECEIVED); 
            servo_arriere_droit(state);
          }
          else 
          {
            write_order(ERROR1); 
          }
        
          break;
        }

        case SERVO_ARRIERE_GAUCHE:
        {

          write_order(RECEIVED); 

          //reads parameter
          int state = get_param();
          Serial.flush(); //avoid multiple instaces of param in serial
          if (state == -1 || state==1)
          {
            write_order(RECEIVED); 
            servo_arriere_gauche(state);
          }
          else 
          {
            write_order(ERROR1);
          }
        
          break;
        }

        case MOTEUR_AVANT_DROIT:
        {

          write_order(RECEIVED); 

          //reads parameter
          int state = get_param();
          Serial.flush(); //avoid multiple instaces of param in serial
          if (state == -1 || state==1)
          {
            write_order(RECEIVED); 
            moteur_avant_droit(state);
          
          }
          else 
          {
            write_order(ERROR1); 
          }
        
        
          break;
        }
        
        case MOTEUR_AVANT_GAUCHE:
        {

          write_order(RECEIVED); 

          //reads parameter
          int state = get_param();
          Serial.flush(); //avoid multiple instaces of param in serial
          if (state == -1 || state==1)
          {
            write_order(RECEIVED); 
            moteur_avant_gauche(state);
          
          }
          else 
          {
            write_order(ERROR1); 
          }
        
        
          break;
        }

        case MOTEUR_ARRIERE_DROIT:
        {

          write_order(RECEIVED); 

          //reads parameter
          int state = get_param();
          Serial.flush(); //avoid multiple instaces of param in serial
          if (state == -1 || state==1)
          {
            write_order(RECEIVED); 
            moteur_arriere_droit(state);
          
          }
          else 
          {
            write_order(ERROR1); 
          }
        
          break;
        }   

        case MOTEUR_ARRIERE_GAUCHE:
        {

          write_order(RECEIVED); 

          //reads parameter
          int state = get_param();
          Serial.flush(); //avoid multiple instaces of param in serial
          if (state == -1 || state==1)
          {
            write_order(RECEIVED); 
            moteur_arriere_gauche(state);
          
          }
          else 
          {
            write_order(ERROR1); 
          }
        
          break;
        }

        case ELECTROAIMANT_AVANT_DROIT:
        {
          write_order(RECEIVED);
          int state = get_param();
          Serial.flush();
          if (state==-1 || state==1)
          {
            write_order(RECEIVED);
            electroaimant_avant_droit(state);
          }
          else
          {
            write_order(ERROR1); 
          }

          break;
        }    

        case ELECTROAIMANT_AVANT_GAUCHE:
        {
          write_order(RECEIVED);
          int state = get_param();
          Serial.flush();
          if (state==-1 || state==1)
          {
            write_order(RECEIVED);
            electroaimant_avant_gauche(state);
          }
          else
          {
            write_order(ERROR1); 
          }

          break;
        }    



        case ELECTROAIMANT_ARRIERE_DROIT:
        {
          write_order(RECEIVED);
          int state = get_param();
          Serial.flush();
          if (state==-1 || state==1)
          {
            write_order(RECEIVED);
            electroaimant_arriere_droit(state);
          }
          else
          {
            write_order(ERROR1); 
          }
          
          break;
        }    


        case ELECTROAIMANT_ARRIERE_GAUCHE:
        {
          write_order(RECEIVED);
          int state = get_param();
          Serial.flush();
          if (state==-1 || state==1)
          {
            write_order(RECEIVED);
            electroaimant_arriere_gauche(state);
          }
          else
          {
            write_order(ERROR1); 
          }
          
          break;
        }    



        // Unknown order
        default:
          write_order(ERROR1);
          return;
      }
      
    }
    
  }
}

int get_param()
{
  unsigned long start_time = millis();
  while(Serial.available() < 1)
  {
    delay(0.1);
    if (millis() - start_time > 3000)
    {
        return ERROR_PARAM; 
    }
  }
  return read_i8();
}

/********************************************
 * 
 * Functions to be called when an order is processed
 * 
 * ********************************************/
void homeMaster()
{

  //homing procedure
  angle = 0;
  home(servomotors,dxl);
  write_order(FINISHED); 
}

void auto_distance(int dist)
{

  //starting procedure to move
  float stepReach = 7.0;
  int walkedDist = 0;

  if(dist>0)
  {
    while(walkedDist<dist)
    {
      robotStep(dxl,1);
      
      walkedDist = walkedDist+stepReach;
    }
  }
  if(dist<0)
  {
    while(walkedDist>dist)
    {
      robotStep(dxl,-1);
      
      walkedDist = walkedDist-stepReach;
    }
  }
  

  write_order(FINISHED); 
  
}

void auto_reverse(int dist)
{

  //stopping procedure to move in reverse
  float stepReach = 7.0;
  int walkedDist = 0;

  if(dist>0)
  {
    while(walkedDist<dist)
    {
      robotStep(dxl,1);
      
      walkedDist = walkedDist+stepReach;
    }
  }
  if(dist<0)
  {
    while(walkedDist>dist)
    {
      robotStep(dxl,-1);
      
      walkedDist = walkedDist-stepReach;
    }
  }
  
  write_order(FINISHED); 
  
}

void set_angle(int ParamAngle)
{
 //utiliser la variable angle pour bouger les servomoteurs
  setAngle(servomotors,dxl, ParamAngle);
  write_order(FINISHED); 
}

void semi_auto_state(int state)
{
  robotStep(dxl,state);
  write_order(FINISHED); 
}
void servo_avant_droit(int state)
{
 digitalWrite(13,LOW);
 delay(200);
 if(state==1)
  {
    angle = angle - angleToAdd;
    servomotors[FRONT_RIGHT_SERVO].write(FRONT_RIGHT_SERVO_HOME + angle);
  }
  else
  {
    angle = angle + angleToAdd;
    servomotors[FRONT_RIGHT_SERVO].write(FRONT_RIGHT_SERVO_HOME + angle);
  }
  digitalWrite(13,HIGH);
  write_order(FINISHED);
}

void servo_avant_gauche(int state)
{
  digitalWrite(12,LOW);
  delay(200);
  if(state==1)
  {
    angle = angle - angleToAdd;
    servomotors[FRONT_LEFT_SERVO].write(FRONT_LEFT_SERVO_HOME + angle);
  }
  else
  {
    angle = angle + angleToAdd;
    servomotors[FRONT_LEFT_SERVO].write(FRONT_LEFT_SERVO_HOME + angle);
  }
   digitalWrite(12,HIGH);
   write_order(FINISHED);  
}

void servo_arriere_droit(int state)
{
  digitalWrite(11,LOW);
  delay(200);
  if(state==1)
  {
    angle = angle - angleToAdd;
    servomotors[REAR_RIGHT_SERVO].write(REAR_RIGHT_SERVO_HOME + angle);
  }
  else
  {
    angle = angle + angleToAdd;
    servomotors[REAR_RIGHT_SERVO].write(REAR_RIGHT_SERVO_HOME + angle);
  }
  digitalWrite(11,HIGH);
  write_order(FINISHED);
}

void servo_arriere_gauche(int state)
{
  digitalWrite(10,LOW);
  delay(200);
  if(state==1)
  {
    angle = angle - angleToAdd;
    servomotors[REAR_LEFT_SERVO].write(REAR_LEFT_SERVO_HOME + angle);
  }
  else
  {
    angle = angle + angleToAdd;
    servomotors[REAR_LEFT_SERVO].write(REAR_LEFT_SERVO_HOME + angle);
  }
  digitalWrite(10,HIGH);
    write_order(FINISHED);
}

void moteur_avant_droit(int state)
{
  digitalWrite(13,LOW);
  delay(200);
  if(state==1)
  {
    if(frontRightMode == RETRACTED)
    {
      raiseFrontRight(dxl, DXL_ID_FRONT_RIGHT);
    }
    else if(frontRightMode == RAISED)
    {
      extensionFrontRight(dxl, DXL_ID_FRONT_RIGHT);
    }
    else if(frontRightMode == EXTENDED)
    {
      nbTurnsFrontRight++;
      retractionFrontRight(dxl, DXL_ID_FRONT_RIGHT);
    }
  }
  else
  {
    if(frontRightMode == RETRACTED)
    {
      nbTurnsFrontRight--;
      extensionFrontRight(dxl, DXL_ID_FRONT_RIGHT);
    }
    else if(frontRightMode == RAISED)
    {
      retractionFrontRight(dxl, DXL_ID_FRONT_RIGHT);
    }
    else if(frontRightMode == EXTENDED)
    {
      raiseFrontRight(dxl, DXL_ID_FRONT_RIGHT);
    }
  }
    write_order(FINISHED);
}

void moteur_avant_gauche(int state)
{
  digitalWrite(12,LOW);
  delay(200);
  if(state==1)
  {
    if(frontLeftMode == RETRACTED)
    {
      raiseFrontLeft(dxl, DXL_ID_FRONT_LEFT);
    }
    else if(frontLeftMode == RAISED)
    {
      nbTurnsFrontLeft++;
      extensionFrontLeft(dxl, DXL_ID_FRONT_LEFT);
    }
    else if(frontLeftMode == EXTENDED)
    {
      retractionFrontLeft(dxl, DXL_ID_FRONT_LEFT);
    }
  }
  else
  {
    if(frontLeftMode == RETRACTED)
    {
      extensionFrontLeft(dxl, DXL_ID_FRONT_LEFT);
    }
    else if(frontLeftMode == RAISED)
    {
      retractionFrontLeft(dxl, DXL_ID_FRONT_LEFT);
    }
    else if(frontLeftMode == EXTENDED)
    {
      nbTurnsFrontLeft--;
      raiseFrontLeft(dxl, DXL_ID_FRONT_LEFT);
    }
  }
    write_order(FINISHED);
}

void moteur_arriere_droit(int state)
{
  digitalWrite(11,LOW);
  delay(200);
  if(state==1)
  {
    if(rearRightMode == RETRACTED)
    {
      nbTurnsRearRight++;
      extensionRearRight(dxl, DXL_ID_REAR_RIGHT);
    }
    else if(rearRightMode == RAISED)
    {
      retractionRearRight(dxl, DXL_ID_REAR_RIGHT);
    }
    else if(rearRightMode == EXTENDED)
    {
      raiseRearRight(dxl, DXL_ID_REAR_RIGHT);
    }
  }
  else
  {
    if(rearRightMode == RETRACTED)
    {
      raiseRearRight(dxl, DXL_ID_REAR_RIGHT);
    }
    else if(rearRightMode == RAISED)
    {
      extensionRearRight(dxl, DXL_ID_REAR_RIGHT);
      
    }
    else if(rearRightMode == EXTENDED)
    {
      nbTurnsRearRight--;
      retractionRearRight(dxl, DXL_ID_REAR_RIGHT);
    }
  }
    write_order(FINISHED);
}

void moteur_arriere_gauche(int state)
{
  digitalWrite(10,LOW);
  delay(200);
  if(state==1)
  {
    if(rearLeftMode == RETRACTED)
    {
      nbTurnsRearLeft++;
      extensionRearLeft(dxl, DXL_ID_REAR_LEFT);
    }
    else if(rearLeftMode == RAISED)
    {
      retractionRearLeft(dxl, DXL_ID_REAR_LEFT);
    }
    else if(rearLeftMode == EXTENDED)
    {
      raiseRearLeft(dxl, DXL_ID_REAR_LEFT);
    }
  }
  else
  {
    if(rearLeftMode == RETRACTED)
    {
      raiseRearLeft(dxl, DXL_ID_REAR_LEFT);
    }
    else if(rearLeftMode == RAISED)
    {
      extensionRearLeft(dxl, DXL_ID_REAR_LEFT);
    }
    else if(rearLeftMode == EXTENDED)
    { 
      nbTurnsRearLeft--;
      retractionRearLeft(dxl, DXL_ID_REAR_LEFT);
    }
  }
    write_order(FINISHED);
}

void electroaimant_avant_droit(int state)
{
  digitalWrite(13,LOW);
  if(state==1)
  {
    digitalWrite(13,HIGH);
  }
  else
  {
    digitalWrite(13,LOW);
  }
    write_order(FINISHED);
}

void electroaimant_avant_gauche(int state)
{
  digitalWrite(12,LOW);
  if(state==1)
  {
    digitalWrite(12,HIGH);
  }
  else
  {
    digitalWrite(12,LOW);
  }
    write_order(FINISHED);
}

void electroaimant_arriere_droit(int state)
{
  digitalWrite(11,LOW);
  if(state==1)
  {
    digitalWrite(11,HIGH);
  }
  else
  {
    digitalWrite(11,LOW);
  }
    write_order(FINISHED);
}

void electroaimant_arriere_gauche(int state)
{
  digitalWrite(10,LOW);
  if(state==1)
  {
    digitalWrite(10,HIGH);
  }
  else
  {
    digitalWrite(10,LOW);
  }
    write_order(FINISHED);
}

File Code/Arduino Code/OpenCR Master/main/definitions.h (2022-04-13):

#if defined(ARDUINO_OpenCR) // When using official ROBOTIS board with DXL circuit.
  // For OpenCR, there is a DXL Power Enable pin, so you must initialize and control it.
  #define DXL_SERIAL   Serial3
  #define DEBUG_SERIAL Serial
  const uint8_t DXL_DIR_PIN = 84; // OpenCR Board's DIR PIN.
#endif

#define FRONT_LEFT_SERVO 0
#define FRONT_RIGHT_SERVO 1
#define REAR_LEFT_SERVO 2
#define REAR_RIGHT_SERVO 3

#define FRONT_LEFT_SERVO_HOME 71
#define FRONT_RIGHT_SERVO_HOME 117
#define REAR_LEFT_SERVO_HOME 126
#define REAR_RIGHT_SERVO_HOME 74

#define PIN_FRONT_LEFT_SERVO_PWM 6
#define PIN_FRONT_RIGHT_SERVO_PWM 3
#define PIN_REAR_LEFT_SERVO_PWM 9
#define PIN_REAR_RIGHT_SERVO_PWM 5

//Movement modes
#define WAIT_MODE 0
#define EXTENSION_MODE 1
#define RETRACTION_MODE 2
uint8_t mode = WAIT_MODE;
using namespace ControlTableItem;

Servo servo_test = Servo();

#define DXL_ID_REAR_LEFT 3
#define DXL_ID_REAR_RIGHT 23
#define DXL_ID_FRONT_LEFT 9
#define DXL_ID_FRONT_RIGHT 22

#define FRONT_LEFT_RETRACTED 2416
#define FRONT_RIGHT_RETRACTED 2835
#define REAR_LEFT_RETRACTED 3140
#define REAR_RIGHT_RETRACTED 864

#define FRONT_LEFT_EXTENDED 400
#define FRONT_RIGHT_EXTENDED 620
#define REAR_LEFT_EXTENDED 827
#define REAR_RIGHT_EXTENDED 3574

#define FRONT_LEFT_RAISED 3209
#define FRONT_RIGHT_RAISED 1661
#define REAR_LEFT_RAISED 1807
#define REAR_RIGHT_RAISED 2363

#define FRONT_RIGHT_PULL_RETRACTED 2350
#define FRONT_LEFT_PULL_RETRACTED 1940 
#define REAR_RIGHT_PULL_RETRACTED 2335
#define REAR_LEFT_PULL_RETRACTED 364

#define FRONT_LEFT_PULL_EXTENDED 4000
#define FRONT_RIGHT_PULL_EXTENDED 120
#define REAR_LEFT_PULL_EXTENDED 327
#define REAR_RIGHT_PULL_EXTENDED 3275

#define PIN_FL_ELECTRO 12
#define PIN_FR_ELECTRO 13
#define PIN_RL_ELECTRO 10
#define PIN_RR_ELECTRO 11

#define RETRACTED 0
#define EXTENDED 1
#define RAISED 2

int angle = 0;
int angleToAdd = 10;

int nbTurnsFrontLeft;
int nbTurnsFrontRight;
int nbTurnsRearLeft;
int nbTurnsRearRight;
int frontLeftMode;
int frontRightMode;
int rearLeftMode;
int rearRightMode;
int objectif;
const float DXL_PROTOCOL_VERSION = 2.0;

bool synchro;

Dynamixel2Arduino dxl(DXL_SERIAL, DXL_DIR_PIN);
Servo servomotors[4] = {};

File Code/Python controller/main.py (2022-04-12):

import sys
import platform
from PyQt5 import QtCore, QtGui, QtWidgets
from PyQt5.QtCore import (QCoreApplication, QPropertyAnimation, QDate, QDateTime, QMetaObject, QObject, QPoint, QRect, QSize, QTime, QUrl, Qt, QEvent)
from PyQt5.QtGui import (QBrush, QColor, QConicalGradient, QCursor, QFont, QFontDatabase, QIcon, QKeySequence, QLinearGradient, QPalette, QPainter, QPixmap, QRadialGradient)
from PyQt5.QtWidgets import *
import communication
from order import Order
import time



# GUI FILE
from ui_main import Ui_MainWindow

class MainWindow(QMainWindow):
    def __init__(self):
        QMainWindow.__init__(self)
        self.ui = Ui_MainWindow()
        self.ui.setupUi(self)
        # self.setWindowModality(QtCore.Qt.ApplicationModal)

        ## For comm
        self.comm = communication.Communication()
        self.listangle = []
        self.listdist = []
        self.listanglerev = []
        self.listdistrev = []

        ## For UI
        self.listcmd = []
        self.counter = 0

        ## PAGES
        ########################################################################

        # PAGE 1
        self.ui.btn_page_1.clicked.connect(lambda: self.ui.stackedWidget.setCurrentWidget(self.ui.page_1))

        # PAGE 2
        self.ui.btn_page_2.clicked.connect(lambda: self.ui.stackedWidget.setCurrentWidget(self.ui.page_2))

        # PAGE 3
        self.ui.btn_page_3.clicked.connect(lambda: self.ui.stackedWidget.setCurrentWidget(self.ui.page_3))

        # Add command button
        self.ui.pb_addcmd.clicked.connect(self.addcmd)

        # Clear command button
        self.ui.pb_clearcmd.clicked.connect(self.clearcmd)

        # Autopage button
        self.ui.pb_home_auto.clicked.connect(self.home_order)
        self.ui.pb_start.clicked.connect(self.start_order)
        self.ui.pb_stop.clicked.connect(self.stop_order)

        # SemiAuto Button
        self.ui.pb_home_semi.clicked.connect(self.homeS_order)
        self.ui.pb_sendcmd.clicked.connect(self.sendcmd_order)
        self.ui.pb_jogf.clicked.connect(self.jogf_order)
        self.ui.pb_jogb.clicked.connect(self.jogb_order)

        # Manual
        ## Step Motors
        self.ui.pb_step_flclock.clicked.connect(self.step_flclock_order)
        self.ui.pb_step_flcounter.clicked.connect(self.step_flcounter_order)
        self.ui.pb_step_frclock.clicked.connect(self.step_frclock_order)
        self.ui.pb_step_frcounter.clicked.connect(self.step_frcounter_order)
        self.ui.pb_step_blclock.clicked.connect(self.step_blclock_order)
        self.ui.pb_step_blcounter.clicked.connect(self.step_blcounter_order)
        self.ui.pb_step_brclock.clicked.connect(self.step_brclock_order)
        self.ui.pb_step_brcounter.clicked.connect(self.step_brcounter_order)

        ## Servo Motors
        self.ui.pb_ser_flclock.clicked.connect(self.ser_flclock_order)
        self.ui.pb_ser_flcounter.clicked.connect(self.ser_flcounter_order)
        self.ui.pb_ser_frclock.clicked.connect(self.ser_frclock_order)
        self.ui.pb_ser_frcounter.clicked.connect(self.ser_frcounter_order)
        self.ui.pb_ser_blclock.clicked.connect(self.ser_blclock_order)
        self.ui.pb_ser_blcounter.clicked.connect(self.ser_blcounter_order)
        self.ui.pb_ser_brclock.clicked.connect(self.ser_brclock_order)
        self.ui.pb_ser_brcounter.clicked.connect(self.ser_brcounter_order)

        ## Magnets
        self.ui.cb_flmag.setChecked(True)
        self.ui.cb_frmag.setChecked(True)
        self.ui.cb_blmag.setChecked(True)
        self.ui.cb_brmag.setChecked(True)
        self.ui.cb_flmag.stateChanged.connect(self.flmag_order)
        self.ui.cb_frmag.stateChanged.connect(self.frmag_order)
        self.ui.cb_blmag.stateChanged.connect(self.blmag_order)
        self.ui.cb_brmag.stateChanged.connect(self.brmag_order)

        ## SHOW ==> MAIN WINDOW
        ########################################################################
        self.ui.stackedWidget.setCurrentWidget(self.ui.page_1)
        self.show()
        self.ui.distance_input.setFocus()
        ## ==> END ##

    ## For UI
    def get_int(self, prompt):
        while True:
            try:
                answer = int(prompt)
                break
            except ValueError:
                return 0
        return 1
    def addcmd(self):
        self.ui.distance_input.setFocus()
        dist = self.ui.distance_input.text()
        angle = self.ui.angle_input_auto.text()
        self.ui.distance_input.repaint()
        self.ui.angle_input_auto.repaint()
        self.ui.distance_input.clear()
        self.ui.angle_input_auto.clear()
        if self.counter == 6:
            self.ui.label_state_auto.setText('List full, clear some command to add others')
            self.ui.label_state_auto.repaint()
            time.sleep(3)

        if self.get_int(dist) == 0 or self.get_int(angle) == 0:
            self.ui.label_state_auto.setText('Please enter an integer value')

        else:
            self.ui.label_state_auto.setText(" ")
            if self.counter < 6:
                self.listcmd.append("Cmd" + str(self.counter + 1) + "-> Dist: " + dist + " Angle: " + angle)
                self.listdist.append(dist)
                self.listangle.append(angle)
                self.counter += 1

            if self.counter == 1:
                self.ui.label_cmd1.setText(self.listcmd[self.counter-1])
            elif self.counter == 2:
                self.ui.label_cmd2.setText(self.listcmd[self.counter-1])
            elif self.counter == 3:
                self.ui.label_cmd3.setText(self.listcmd[self.counter-1])
            elif self.counter == 4:
                self.ui.label_cmd4.setText(self.listcmd[self.counter-1])
            elif self.counter == 5:
                self.ui.label_cmd5.setText(self.listcmd[self.counter-1])
            elif self.counter == 6:
                self.ui.label_cmd6.setText(self.listcmd[self.counter-1])
    def clearcmd(self):

        if self.counter > 0:
            self.listcmd.pop()
            self.listdist.pop()
            self.listangle.pop()

        if self.counter == 1:
            self.ui.label_cmd1.setText(" ")
        elif self.counter == 2:
            self.ui.label_cmd2.setText(" ")
        elif self.counter == 3:
            self.ui.label_cmd3.setText(" ")
        elif self.counter == 4:
            self.ui.label_cmd4.setText(" ")
        elif self.counter == 5:
            self.ui.label_cmd5.setText(" ")
        elif self.counter == 6:
            self.ui.label_cmd6.setText(" ")

        if self.counter > 0:
            self.counter -= 1

    ## Orders
    # Automatic
    def home_order(self):
        self.setEnabled(False)
        self.ui.label_state_auto.setText('Homing...')
        self.ui.label_state_auto.repaint()
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

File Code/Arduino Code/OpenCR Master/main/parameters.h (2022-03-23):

#ifndef PARAMETERS_H
#define PARAMETERS_H

#define SERIAL_BAUD 115200  // Baudrate
#define MOTOR_PIN 3
#define DIRECTION_PIN 4
#define SERVOMOTOR_PIN 6
#define INITIAL_THETA 110  // Initial angle of the servomotor
// Min and max values for motors
#define THETA_MIN 60
#define THETA_MAX 150
#define SPEED_MAX 100

// If DEBUG is set to true, the arduino will send back all the received messages
#define DEBUG false

#endif

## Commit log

2022-02-06 Arduino code foundation
2022-02-09 Update and rename Protoypes préliminaires to Preliminary prototypes
2022-02-11 Add files via upload
    proto frame v1
    [frame.SLDPRT, mount_servo.SLDPRT]
2022-02-13 Add files via upload
    pieces patte proto complet 1
    [beam1.STL, beam2.STL, beam3.STL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]
2022-02-14 Move libraries to src repo
    [opencr_flash.cfg, opencr_openocd.cfg]
2022-02-16 include path changes
    [opencr_flash.cfg, opencr_openocd.cfg]
2022-02-19 Manual Page + Button test
2022-02-20 Established a communication protocol between pc and arduino
2022-02-21 New velocity_mode test
2022-02-22 Home button UI
2022-02-23 add communication files to python controller and update arduino com
2022-03-09 prevent letters to be typed
    [main.py]
2022-03-21 Create Test_proto_board.ino
    Create test program for the electromagnets while connected to the protoboard and an arduino mega
2022-03-23 Create Nano_code_for_magnet.ino
    Nano code to transfer 3.3v to 5v for magnet
2022-03-30 UI+arduino test
2022-04-12 magnets changes
